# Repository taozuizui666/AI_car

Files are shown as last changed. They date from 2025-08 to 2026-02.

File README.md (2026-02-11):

# **AI\_car**

*a self-driving car project based on AI model*

author ： TAO RAN

### **note**：

1. when compilation wrong in ardunio, try remove C\\...\\AppData\\Local\\arduino\\sketches files, this may make recompile successful.
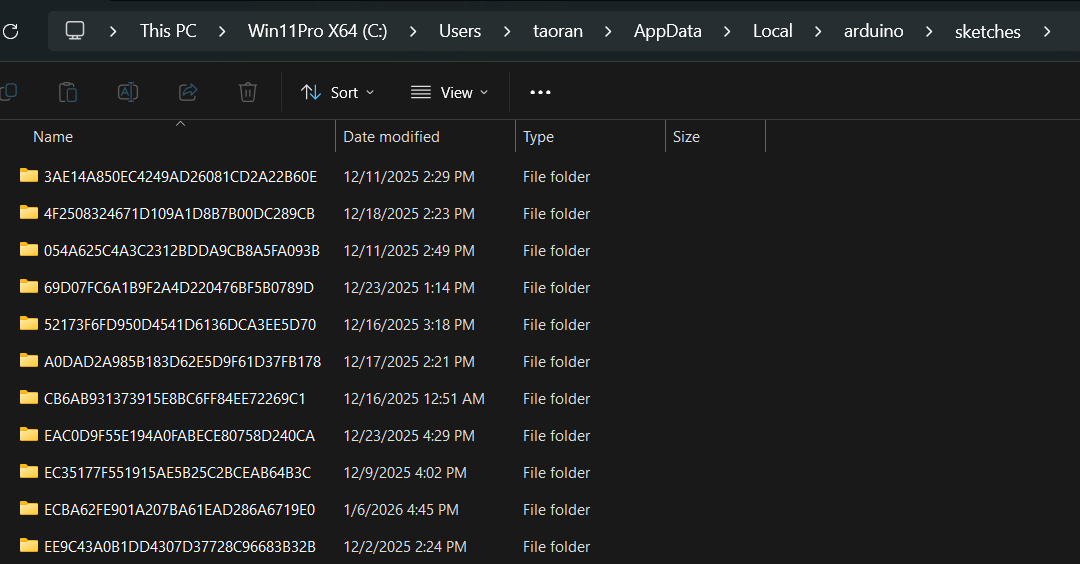
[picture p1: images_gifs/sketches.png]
sketches

2. if you cannot store file into SD card or the file you stored is always damaged, scan your SD card's file first, if there is any damaged file like with data 2049 or the size is extremely large like 2097153KB, then delete this file. Any damaged file inside your SD card will very likely to lead to the above situation
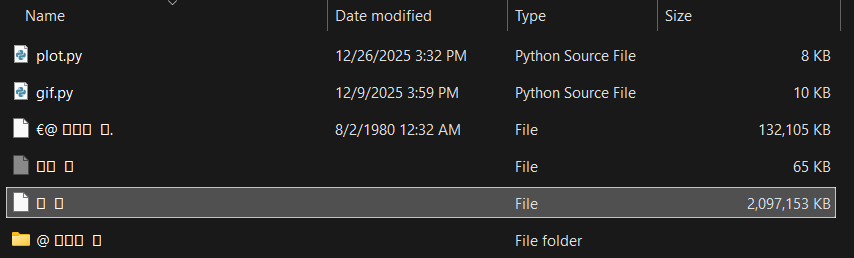
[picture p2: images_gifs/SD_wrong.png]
like this


##
version v1.0.0

the whole program is divided into 3 main parts : 
* **part1**: build the car and run program (bluetooth control, Lidar scan and SD store )
* **part2**: train the car through App on the phone
* **part3**: use ML methods to train a model to enable the car self-control

##
version v2.0.0
following improvements:
* **part1**: using digital tween for trainning(python/ gazebo/ stage),because it's more efficient to use computer to virtually train the car, let alone some complex situations like overtake another car, it's very hard to train this manually, and the trainning data we need is very large.

## 

### **program code address** :
teensy_project\C_code\AIcar\main_lidar_SD_test -now yield really now\main
### **App address** :
teensy_project\Androidapp\App

##

record : after 3 months(2025.08.04-2025.11.30), the car can use store lidar's data into SD now.

I'll briefly introduce the Part1's work first.

I designed an APP that can control the car by slider through bluetooth(which is a very common way):
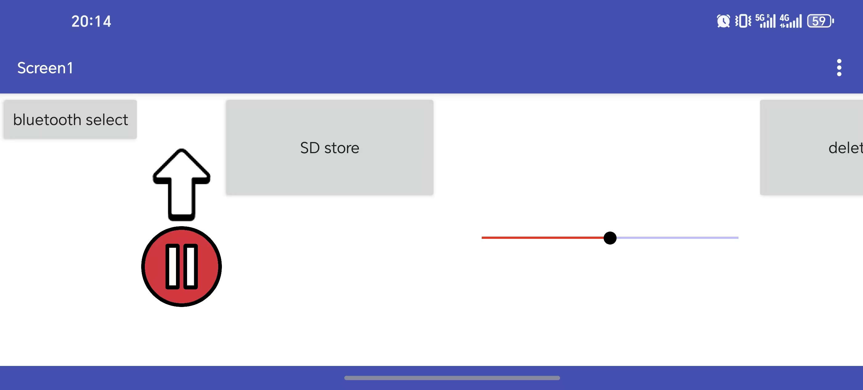
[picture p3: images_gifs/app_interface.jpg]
app


the slider has 21 steps, from 0 to 20. In my configuration, 10 stands for going forward(means slider is in the middle of the line, like now), and 0 means left turn limit, and 21 means right turn limit. You can see the settings of this APP below:
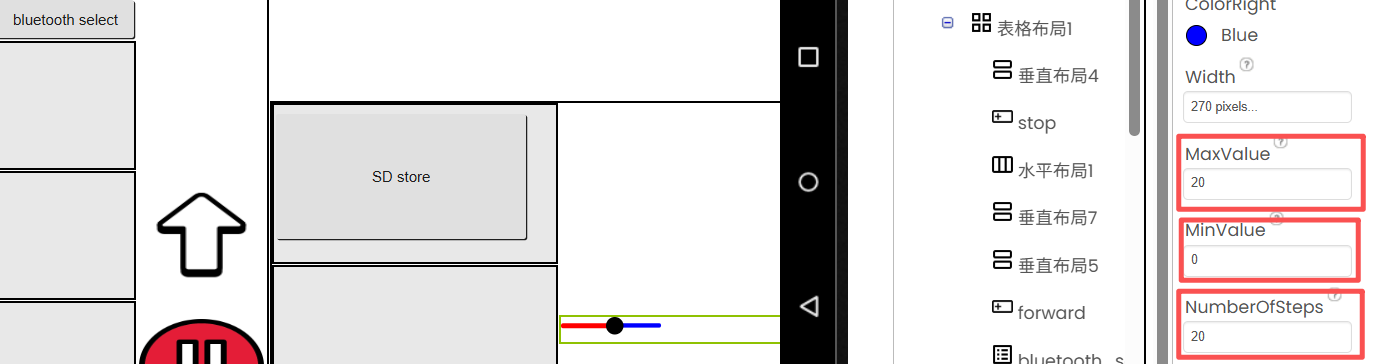
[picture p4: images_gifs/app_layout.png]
app_setting

The phone will send the postion of slider to the car's receiver through bluetooth(it's obvious in the designer diagram below). Addtionally, there are 4 another unique numbers:[200,201,254,255]   stands for 'stop','forward','delete_file','SD_store' respectively. You can see my Designer diagram below:

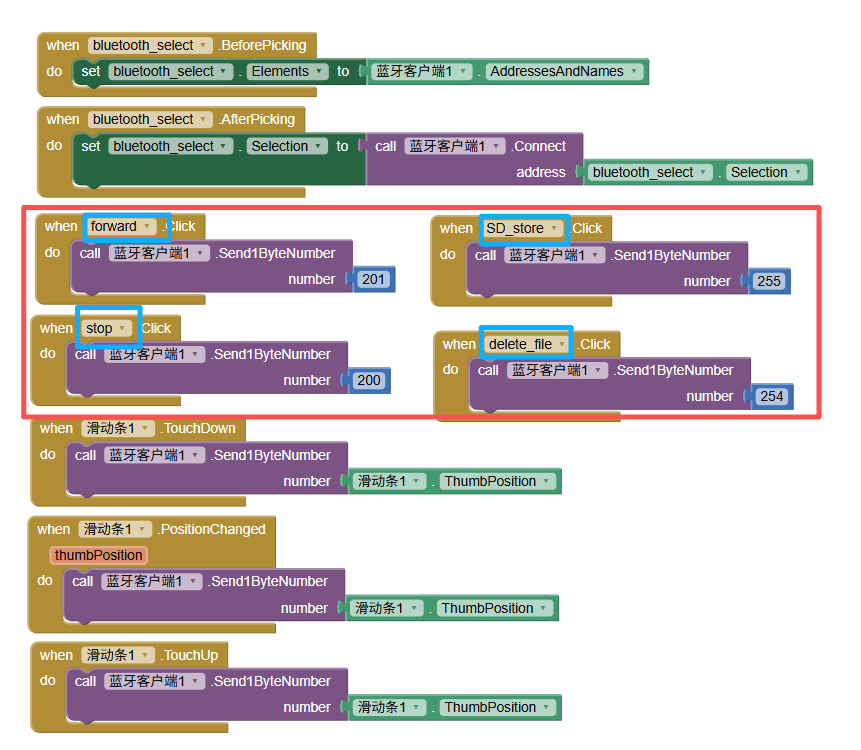
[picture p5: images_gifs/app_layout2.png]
unique_num


When the car receive the data, I wrote a function to handle it. You can ignore the bias now, it's for adjusting left and right motos.

```

void slide_control(int receive_bt,int v_car,int left_moto,int right_moto,int sensi)
{
    switch(receive_bt){
        case 200:
            stop_CS(left_moto,right_moto);
            break;
        case 201:
            ahead_CS(v_car,left_moto,right_moto);
            break;
        case 255:
            break; // start SD store
        default:
            analogWrite(left_moto,bias + v_car-(10-receive_bt)*sensi);
            analogWrite(right_moto, v_car+(10-receive_bt)*sensi);
            break;
    }
}

```

it took me less than 1 month to complete 90% of Part1, but it took me more than 2 months to complete the last 10%. I can't use the [rplidar library](https://github.com/robopeak/rplidar_arduino) on teensy board, so I just read the manual and use my own code to analyse data from the rplidar.

It is very strange that when I use computer to receive data from Lidar, it is all ok, when I store data into SD card, it is all ok too no matter how many data I stored one time( you can see the codes in the C_code folder), but when I combined them together, there are strange errors all the time,  like: reset the chip after 5-10s, file remains empty, can't control the car after 5-10s ...

I think SD's base communication -- SPI is too slow, so when storing data into SD, it block the CPU from getting and processing with Lidar data, but Lidar data is very huge and fast, this could make the data buffer(the place to store received data from Lidar) collapse after few rounds of storing to SD.

I should use DMA to directly store data into SD, this can make CPU easy to work on Lidar's data processing and bluetooth. But I failed to configure DMA on teensy4.0, I think you can solve the previous problem by using DMA method.

now I am using "yield()" function to handle this, "yield()" can stop the current process, check USB message and reset the watch_dog timer. it is said in these way can handle the chip reset problem and it dose, but I still don't know whether it is the true reason, later I will do other experiences to research this.
```
for(int i=0; i<num_of_round; i++){
  f.print(Lidar_list_dis[i]);
  f.print(',');
  // every storing 50 data, reset the watch_dog timer to tell the system is all OK
  if (i % 50 == 0) yield(); 
}

```

another important method I use is to clean the Lidar_data buffer after storing data to SD, to prevent the buffer collapse after been blocked for so long .

```
//-----codes that store data to SD-----

while(Serial2.available()) {
  Serial2.read(); 
}

```
This make me learn a lesson: we shouldn't just go after the speed, we should also take stability into consideration. Dr. Gerard told me sometimes it's very useful to make the fast process wait sometime for the slow process.

##

I tried Ardunio UNO these days, and it surprised me that it can use [rplidar library](https://github.com/robopeak/rplidar_arduino)! although RAM is very small(2KB), with the library, data stored in SD card is much more smooth than teensy4.0. 

By using the library, it works well, to test whether this method can work, I started with trainning the car go anticlockwise, to verify the data good or not, I wrote a python code to translate the data at each angle in each round of lidar to the scatter diagrams in the polar map, you can see clearly the surroundings of the car.

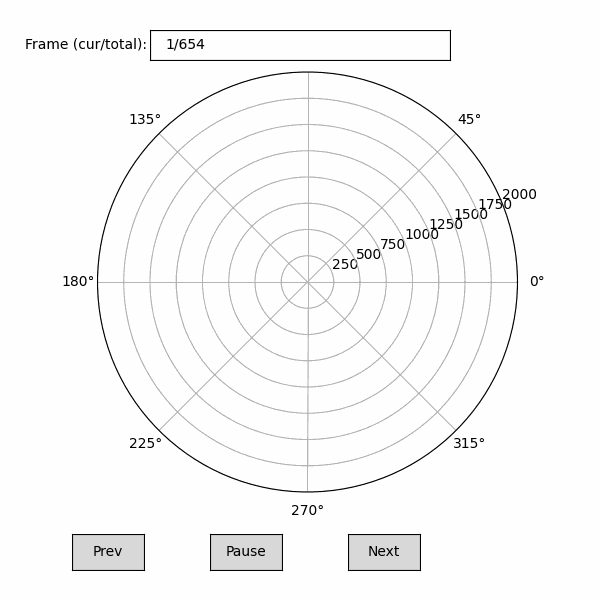
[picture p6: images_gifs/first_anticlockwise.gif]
scatter diagram


But there are also some problems:
* some edges are empty, some points are missing(means 0s)
0s
* the diagram blinks sometimes(in fact often), it means wrong numbers like '?' or something else or the number of one line is not the same as we set
wrongnums
wrongnums

I will try to solve this problem later.

Doc. Gerard told me I don't have to collect data that are behind the car, it goes forward and judges the direction only based on forward informations. so I modifed the code and later on, all diagrams will have points only at angles [0,90]&[270,360]

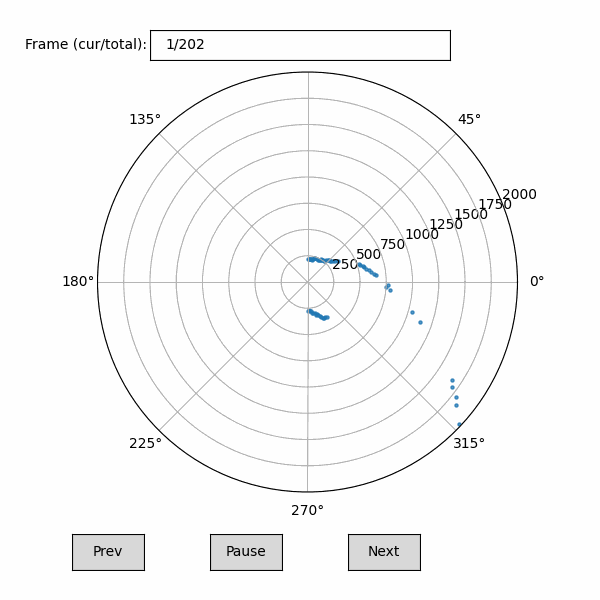
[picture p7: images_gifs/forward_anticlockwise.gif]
forward


I collected data of 5492KB, and merge these files into one, after clean the wrong lines(including wrong numbers and lines that are not full), I got data of 5116KB 
datasize
##
Then I move to the next step --> train a ML model

I use RandomForestClassifier from sklearn for trainning, and select 12 best index from 100 index, we can see these index marked red below:

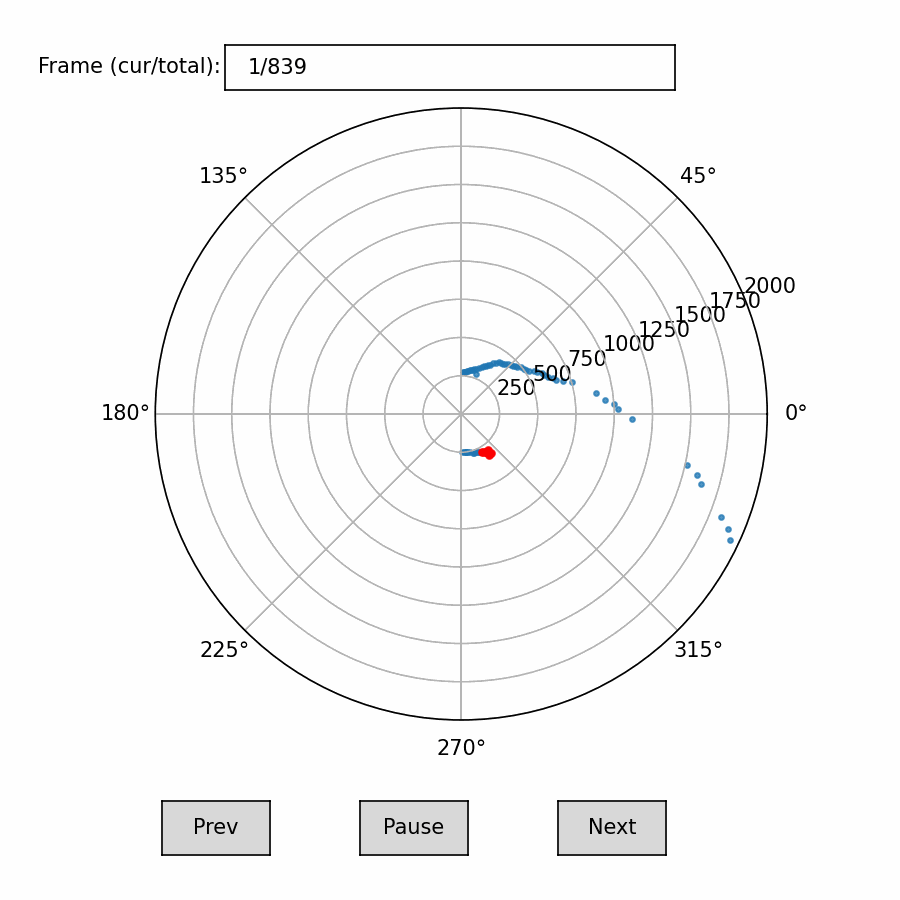
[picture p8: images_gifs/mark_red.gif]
marked red


 and follow the conventional routine, considering the ROM is only 2MB, I set max_depth=3 and n_estimators=50(if I choose max_depth=4, the ROM will be overwhelmed), 
```
k = 12
k_best = SelectKBest(score_func=f_classif, k=k)
k_best.fit(X_train, y_train)

clf = RandomForestClassifier(
    n_estimators=50,
    max_depth=3, 
    random_state=42)
```
then I calculate the accuracy, superisingly, it's 0.1954!!!

I checked the [YouTuber's work](https://github.com/robopeak/rplidar_arduino), he collected data at most 17780KB, but it's many different ways like '8',clockwise, anticlockwise and so on, I don't think my dataset has such a low accuracy. When I saw he only got 5 directions:

 (forward, a bit left, very left, a bit right, very right)

 I suddenly understand why. I have 21 directions!(from 0 to 20,10 stands for go forward) it means that 10 is nearly no difference with (11,12) and (9,8), and some differece with (13,14) and (7,6). so if the ML model predicts the direction is 10, and the real direction is 9 or 12 in the test_set, it shouldn't be wrong! when I include this ±2 to be correct, the accuracy increased crazily to 80%! I know there are some problem with this method, but it shows the model is not that bad, and let's look at the result. It can automaticly drive itself anticlockwise!

##

I modified the library and made it work on teensy4.0 now. in the library, there are some codes can resolve the noise problem, which is very important in this high speed module. I think that is why my data stored in SD card may stuck after a few seconds. now I solved this, with large RAM on teensy4.0, data is even more smooth than on Ardunio UNO.

##
I'm going to use Raspberry Pi 4.0 to drive the Rplidar later, because the official's SDK supports ROS, and it's easy to use Gazibo for digital tween in ROS. So later the version would be v2.0.0.

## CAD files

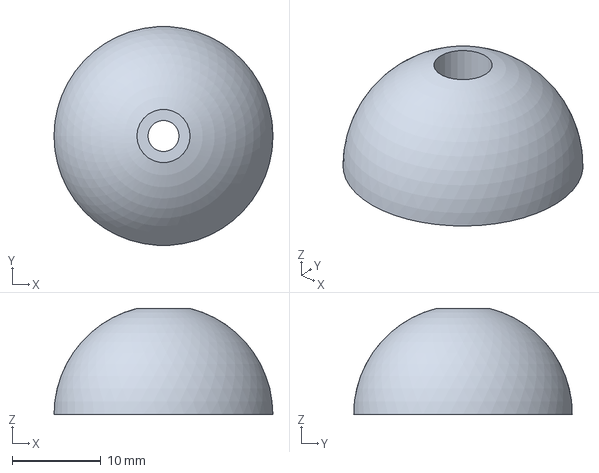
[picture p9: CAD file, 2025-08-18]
hardware/3Dmodels/caster_wheel.3mf
24.7 x 24.7 x 12.0 mm

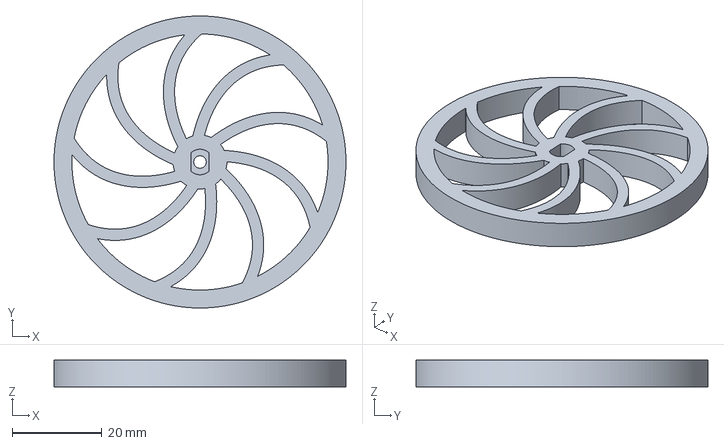
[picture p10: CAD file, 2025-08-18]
hardware/3Dmodels/nikodembartnik-11-tt_motor_wheel.3mf
65.0 x 65.0 x 6.00 mm

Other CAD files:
hardware/3Dmodels/holder_16pair.gcode.3mf
hardware/3Dmodels/holder.gcode.3mf
hardware/3Dmodels/nikodembartnik-48-rplidar_holder.gcode.3mf
hardware/3Dmodels/zhijia.gcode.3mf
hardware/3Dmodels/zhijia2.gcode.3mf
hardware/3Dmodels/motor_holder_right.gcode.3mf

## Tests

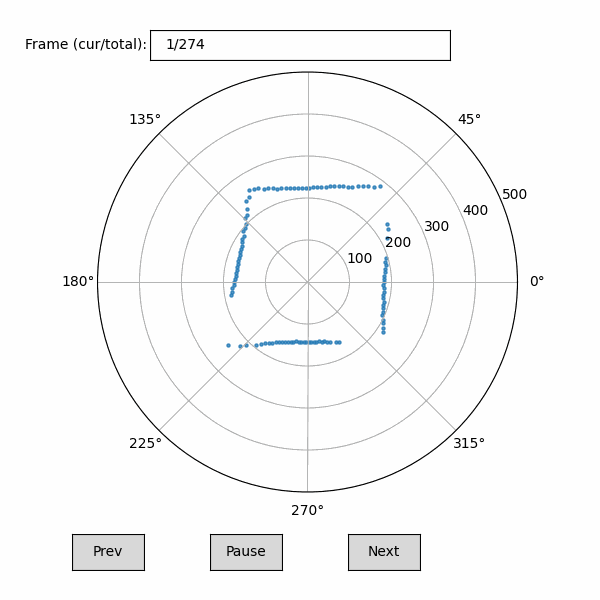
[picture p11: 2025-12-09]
software/test/lidar_animation1.gif

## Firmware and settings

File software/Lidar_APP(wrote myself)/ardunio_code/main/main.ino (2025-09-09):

#include <SoftwareSerial.h>
#include <SPI.h>
#include <SD.h>
#include "control_slide.h"
#include "SD_card.h"
// ports
#define Lidar_TX    7   //teensy RX2
#define Lidar_RX    8   //teensy TX2
#define Lidar_ctr   9   //control the spin speed of lidar
#define CS          10  //chip select(from SD_card module)
#define MOSI        11
#define MISO        12
#define SCK         13  //serial clk(from SD_card module)
#define LEFT_MOTO   14
#define RIGHT_MOTO  15
// paras
#define SCK_MHZ     10  // 10HZ
#define baud        115200
#define baud2       115200
#define bufsize     256       // SD_card's buf size
#define V_car       200       // velocity of the car
#define Sensi       1         // sensitivity of control ; bigger than more sensitive
#define Lidar_head_num      7     //A5 5A 05 00 00 40 81 
#define Lidar_data_bin_num  5
#define num_of_round        320   // the number of data after a round

//-------------bluetooth----------------
//// connect bluetooth to the board
SoftwareSerial bluetooth(0,1);  // bluetooth's pin RX,TX
int receive_bt = 0;             // data received from bluetooth
//-------------SD_card------------------
////attention ! File is not FILE
File f;
//-------------lidar_data---------------
bool Lidar_head_message;
bool new_start;                 // a round is finished
int  Lidar_list_index;
unsigned char   Lidar_data;
unsigned char   Lidar_init[Lidar_head_num];
unsigned char   Lidar_5byte[Lidar_data_bin_num];
unsigned char   Lidar_list[num_of_round*Lidar_data_bin_num];

//// millis time
unsigned long start_time;
const unsigned long runtime = 30*60*1000;

#define Method  2

void setup() {
  start_time = millis();
  //-------------Lidar---------------------
  //// connect RX2/TX2 to lidar's RX/TX
  Serial2.begin(baud2);
  //// turn on the lidar to receive data
  //// attention! lidar can only receive data when it is spinning

  Serial2.write(0xA5);
  Serial2.write(0x20);  
  //-------------pin outputs---------------
  pinMode(Lidar_ctr, OUTPUT);
  pinMode(CS, OUTPUT);
  pinMode(MOSI, OUTPUT);
  pinMode(SCK, OUTPUT);
  pinMode(LEFT_MOTO,OUTPUT);
  pinMode(RIGHT_MOTO,OUTPUT); 

  //// control the spin speed of lidar
  analogWrite(Lidar_ctr, 255);  
  //-------------bluetooth----------------
  bluetooth.begin(baud);  // bluetooth's 波特率
  //-------------SD_card------------------
  // SD_module_init(CS);     // initialize the SD_module and create Folder 
  // if(!SD.exists("Database/data0.txt"))
  // {
  //   f = SD.open("Database/data0.txt",FILE_WRITE);
  //   if(f){
  //     f.close();
  //   }
  // }
  //------------test lidar's data--------
  Serial.begin(baud);
  Lidar_head_message=0;
  new_start = 0;
  Lidar_list_index = 0;
  //-------------end of setup()-----------
}

void loop() {
  if(millis()-start_time < runtime){
    //-------------bluetooth----------------
    //// use bluetooth to control the car
    // if(bluetooth.available())
    // {
    //   receive_bt = bluetooth.read();
    //   slide_control(receive_bt,V_car,LEFT_MOTO,RIGHT_MOTO,Sensi);
    //   if(receive_bt==200)// when control_signal is "stop",then stop both car and lidar
    //   {Serial2.write(0xA5);
    //     Serial2.write(0x25);}
    // }
    if((!Lidar_head_message)&&(Serial2.available()==Lidar_head_num))
    {
      for(int i=0;i<Lidar_head_num;i++)
      {
        Lidar_data = Serial2.read();
        Serial.write(Lidar_data);
      }// release the reading buff, otherwise the message will stay in the buff
      Lidar_head_message = 1;
    }
    //--------------------------------------------------------
    //--------------------------------------------------------
    //// write data for a hole circle(each angle has 5byte data)
#if Method==1    
    while(new_start != 1)
    {
      if(Lidar_head_message && Serial2.available()>=Lidar_data_bin_num)
      {
        for(int i=0;i<Lidar_data_bin_num;i++,Lidar_list_index++)
        {
          Lidar_5byte[i] = Serial2.read();
          Lidar_list[Lidar_list_index] = Lidar_5byte[i];
        }
        if((Lidar_5byte[0] & 0x01) == 1)
        {
          new_start = 1;
        }
      }
    }
    f = SD.open("Database/data0.txt",FILE_WRITE);
    for(int i=0;i<Lidar_list_index;i++)
    {
      // Serial.write(Lidar_list[i]);
      //// Serial.print(Lidar_list[i]);
      ////----------write Lidar_list data to SD_card--------------
      f.print(Lidar_list[i]);
      f.print(",");
    }
    f.print("\n");
    f.close();
    Lidar_list_index = 0;
    new_start = 0;
    //--------------------------------------------------------
    //--------------------------------------------------------
#elif Method==2
    if(Lidar_head_message && Serial2.available()>=Lidar_data_bin_num)
    {
      for(int i=0;i<Lidar_data_bin_num;i++)
      {
        Lidar_5byte[i] = Serial2.read();
      }
      for(int i=0;i<Lidar_data_bin_num;i++)
      {
          Serial.write(Lidar_5byte[i]);
      } 
    }
#else

#endif
  //---------------big if---------------------  
  }else{
    analogWrite(Lidar_ctr,0);
    while(1);
  }
  //--------------end of loop()-------------
}

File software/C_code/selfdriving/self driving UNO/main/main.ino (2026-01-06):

#include <SoftwareSerial.h>
#include <RPLidar.h>
#include "control_slide.h"
#include "randomForest.h"

// ports

#define Lidar_ctr     8   //control the spin speed of lidar 
#define LEFT_MOTO     9
#define RIGHT_MOTO    6

// paras
#define serial_baud         115200
#define lidar_baud          115200
#define V_car               100       // velocity of the car
#define Sensi               1         // sensitivity of control ; bigger than more sensitive

#define degree_90           LIDAR_RESOLUTION/4
#define degree_270          3*LIDAR_RESOLUTION/4
#define LIDAR_RESOLUTION    200
#define time_of_round       150     ////-------------------about 147 ms a round------------------
#define k_best              8

//-------------Lidar--------------------
RPLidar lidar;
uint16_t distances[LIDAR_RESOLUTION];
Eloquent::ML::Port::RandomForest clf;

int lidarDataSelection[k_best] = {22, 23, 24, 25, 26, 27, 28, 29};

long last_time = 0;
uint8_t ML_contr=0;

void setup() {  

  for (int a = 0; a < LIDAR_RESOLUTION; a++) {
    distances[a] = 0;
  }
  lidar.begin(Serial);
  //-------------pin outputs---------------
  pinMode(Lidar_ctr, OUTPUT);
  pinMode(LEFT_MOTO, OUTPUT);
  pinMode(RIGHT_MOTO, OUTPUT);

  rplidar_response_device_info_t info;
  if (IS_OK(lidar.getDeviceInfo(info, 100))) {
      lidar.startScan();
      analogWrite(Lidar_ctr, 255);
      delay(1000);
  }
  last_time = millis();
  //---------------end of setup------------------
}

void loop() {
  while(millis() - last_time <= time_of_round){
    lidar.waitPoint();
    uint16_t dist = (uint16_t)lidar.getCurrentPoint().distance;
    uint16_t angl = (uint16_t)lidar.getCurrentPoint().angle;
    // uint16_t qual = (uint16_t)lidar.getCurrentPoint().quality;
    int index = (int)((angl / 360.0f) * (float)LIDAR_RESOLUTION);

    if((index<degree_90)||(index>degree_270)){
      if (dist<10000) {
        distances[index] = (uint16_t)dist;
      }else{}
    }
  }

  float selectedData[k_best];
  for (int i = 0; i < k_best; i++) {
    selectedData[i] = distances[lidarDataSelection[i]];
  }  

  ML_contr = clf.predict(selectedData);
  slide_control(ML_contr, V_car, LEFT_MOTO, RIGHT_MOTO, Sensi);

  // while (Serial.available()) {
  //   Serial.read();
  // }

  last_time = millis();
}

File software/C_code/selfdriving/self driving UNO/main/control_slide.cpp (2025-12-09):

#include "control_slide.h"
#define bias    31
void stop_CS(int left_moto,int right_moto)
{
    analogWrite(left_moto, 0);
    analogWrite(right_moto, 0);    
}

void ahead_CS(int v_car,int left_moto,int right_moto)
{
    analogWrite(left_moto, v_car );
    analogWrite(right_moto, v_car+ bias);
}

void slide_control(int receive_bt,int v_car,int left_moto,int right_moto,int sensi)
{
    switch(receive_bt){
        case 200:
            stop_CS(left_moto,right_moto);
            break;
        case 201:
            ahead_CS(v_car,left_moto,right_moto);
            break;
        case 255:
            break; // start SD store
        default:
            analogWrite(left_moto, (int)(v_car-(10-receive_bt)*sensi*3));
            analogWrite(right_moto, bias + v_car+(10-receive_bt)*sensi);
            break;
    }
}

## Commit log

2025-08-18 first git
    [Untitled.gcode.3mf, caster_wheel.3mf, caster_wheel.step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]
2025-08-19 now the board can receive data from Lidar and store the data into SD_card
    [nikodembartnik-10-connector_40mm.3mf, nikodembartnik-98-distance_HS_55mm.stl, ran.csv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]
2025-08-28 upload a video of controlling the car with bluetooth
    [holder.3mf, holder.gcode.3mf, holder_16pair.gcode.3mf]
2025-08-31 rename the folders and optimze the file constructures
    [holder.3mf, ran.csv]
2025-09-04 test lidar
2025-09-05 create a python program to display lidar's data in a polar coordinates
2025-09-09 Lidar APP which wrote myself can scan the arround environment like the official APP does
2025-09-23 main_lidar_SD_Done_0 is uploaded, this can store angles and distance of the lidar into SD card with little mistakes
    [control_slide.cpp, main.ino]
2025-10-17 solve the delay problem of bluetooth module, it's the baud, it should be 9600 for the best performance, but we set it to 115200 previously, it's too large for out bluetooth module
    [2test_serial.py, control_slide.cpp, main.ino]
